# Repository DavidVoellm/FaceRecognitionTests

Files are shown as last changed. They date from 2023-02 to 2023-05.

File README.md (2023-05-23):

# **HAUS MIT SICHERHEITSTÜR**

NwT-Abschlussprojekt J2

Teilnehmer: Mona Endreß, Lutz Engler, Max Stacherowski, David Völlm

Zeitraum: 06.02.2023-22.05.2023



## **INHALTSVERZEICHNIS**

1. **Einleitung**                                                       3
1. **Vorbereitungsphase**                                               4
   1. Projektauftrag                                                    4
   1. Projektziele                                                      4
1. **Planungsphase**							                                 4
   1. Projektstrukturplan/ Arbeitspakete                                4
   1. Projektzeitplan                                                   5
   1. Recherche                                                         5
   1. Bauteile                                                          6
   1. Schaltung                                                         6
1. **Durchführungsphase**                                               7
   1. Funktionsbeschreibung                                             7
   1. Ablauf                                                            7
   1. Anhänge                                                           8
   1. Aufgabenbereiche                                                  8
1. **Abschlussphase**                                                   9
   1. Ist-Soll-Vergleich                                                9
   1. Fehleranalyse/ Verbesserungsvorschläge                            9
   1. Zusammenfassung/ Resümee                                          10
1. **Quellenangaben**                                                   10
   1. Literaturverzeichnis                                              10
   1. Internetquellenverzeichnis                                        10

##    **1. EINLEITUNG**

Wir wollen ein Miniaturhaus mit einer Sicherheitstüre bauen. Diese soll nur aufschließen, wenn eine Person anhand eines Gesichtserkennungsprogramms erkannt wird. 

Die Sicherheit und Privatsphäre gewann in den letzten Jahren immer mehr an Wichtigkeit und ist ein relevantes Thema für die Zukunft. Durch das wachsende Bewusstsein des Ersetzens von „altmodischen“ Begebenheiten durch neue Technologien, ist ein Fortschritt in allen Lebenssituationen unabdingbar. Das Leben der Menschen so effizient und unkompliziert wie möglich zu gestalten ist ein wichtiger Faktor im privaten Sektor. Bereits seit ein paar Jahren ist die Gesichtserkennung immer mehr bei Smartphones, Tablets usw. vertreten. Aber auch auf politischer, wirtschaftlicher und gesellschaftlicher Ebene gewinnt die künstliche Intelligenz beziehungsweise die Gesichtserkennung immer mehr an Bedeutung. So wird diese zum Beispiel für Massenüberwachungen, Zugangskontrollen oder die Suche nach Straftätern verwendet.  

1966 erschuf Woodrow „Woody“ Wilson Bledsoe eine Rechenmaschine, die „Computer-Person“, die die Anfänge der Gesichtserkennung mit Hilfe der künstlichen Intelligenz markierte. Das Grundprinzip einer solchen Maschine besteht daraus ein spezifisches Muster aus Bildern herauszufiltern und anschließend in binäre Codezeilen umzurechnen. Daraufhin wird diese Code-Kette mit einer Datenbank abgeglichen und über einen anderen Mechanismus an den Verbraucher signalisiert. Bei Woody zum Beispiel über einen angeschlossenen Ohrknopf. [\[1\]](https://www.boonedam.de/blog/das-gesicht-der-zukunft-erkennen#_ftn1) [\[4\]](https://www.boonedam.de/blog/das-gesicht-der-zukunft-erkennen#_ftn1) Das heißt die Gesichtserkennung ist kein neues Phänomen, sondern schon seit Jahrzehnten im stetigen Wandel. Nur hat sich die Funktionsweiße der Gesichtserkennung immer weiterentwickelt.

AnyVision ist der weltweit führende Entwickler von Computer Vision Software mit künstlicher Intelligenz für die Gesichtserkennung. „Die Mission von AnyVision ist es, künstliche Intelligenz weltweit zugänglich zu machen. Auf diese Weise entsteht ein Netzwerk intelligenter Geräte und setzt neue Standards für die Sicherheit in der Welt um uns herum“, erklärt Ray Brancato, Chief Revenue Officer bei AnyVision. [\[2\]](https://www.boonedam.de/blog/das-gesicht-der-zukunft-erkennen#_ftn1) So schön dieses Zitat von AnyVision klingt, die Gesichtserkennung hat auch ihre Schattenseiten. Regierungen können ihre Bevölkerung überwachen und kontrollieren und ein Verlust von Privatsphäre kann verstärkt auftreten. Ein Beispiel hierfür wäre China, wo Datenschutz über keine sonderliche Relevanz verfügt und die Bevölkerung quasi durchgehend überwacht wird. [\[3\]](https://www.boonedam.de/blog/das-gesicht-der-zukunft-erkennen#_ftn1) Auch sind Computersysteme im Vergleich zu Schlüssel und Schloss anfällig für Hackerangriffe. 

Deshalb möchten wir uns mit diesem Projekt damit beschäftigen die Gesichtserkennung so zu verwenden, dass die Privatsphäre der Menschen steigt und gleichzeitig eine Vereinfachung des Lebens stattfindet.

##    **2. VORBEREITUNGSPHASE**

### **2.1. Projektauftrag**

In einer Gruppe (2er-4er Teams) wird bis zum 22.05.2023 ein technisches Gerät entwickelt.

Das Projekt wird am 22.05.2023 präsentiert und die Dokumentation am 15.05.2023 fertiggestellt, ausgedruckt, digital und persönlich abgegeben. Ein erster Dokumentationsentwurf wird am 31.03.2023 abgegeben.

### **2.2. Projektziele**

Ein Haus mit Sicherheitstür soll erstellt werden. Die Tür kann nur durch ein Gesichtserkennungsprogramm nach außen geöffnet werden. Ein Knopf („Klingel“) startet das Programm und bei Erkennung einer Person öffnet sich das Schloss. Eine LED sowie ein Tonsignal eines Buzzers sollen angeben ob das Gesicht erkannt wurde und die Person berechtigt ist durchzugehen. 

##    **3. PLANUNGSPHASE**

### **3.1. Projektstrukturplan**



### **3.2. Projektzeitplan**

||<p>Woche 1</p><p>6/9.2.23</p>|<p>Woche 2</p><p>13/16.2.23</p>|<p>Woche 3</p><p>27\.2/2.3.23</p>|<p>Woche 4</p><p>6/9.3.23</p>|<p>Woche 5</p><p>13/16.3.23</p>|<p>Woche 6</p><p>20/23.3.23</p>|<p>Woche 7</p><p>27/30.3.23</p>|<p>Woche 8</p><p>8/11.5.23</p>|
| :- | :- | :- | :- | :- | :- | :- | :- | :- |
|Planung, Ideen|x|x|||||||
|**Programmierung**||x|x|x|x|x|x||
|Kamera|||x||||||
|**CAD**||x||x||x|x||
|**Dokumentation**|||x||||x|x|
|Testen||||||x||x|
|Sägen; Bohren|||||x||x||
|Zusammenbau||||||||x|
|Knopf||||||||x|

|**ABGABE**|<p>31\.03.2023</p><p>(Entwurf Dokumentation)</p>|<p>15\.05.2023</p><p>(Dokumentation)</p>|<p>22\.05.2023</p><p>(Präsentation)</p>|
| :-: | :-: | :-: | :-: |

### **3.3. Recherche:**

**Raspberry Pi: [\[5\]](https://www.boonedam.de/blog/das-gesicht-der-zukunft-erkennen#_ftn1)**

Der Raspberry Pi ist ein kostengünstiger (ca. 40€) kleiner Computer. Da er leider aktuell nicht mehr produziert wird, sind die wenigen übrigen Exemplare sehr teuer. Er wurde für die Universität Cambridge von der Raspberry Pi Foundation entwickelt. Es handelt sich um einen Einplatinen-Computer, der über kein Netzteil verfügt. Das passende Betriebssystem sind die Linux Distributionen.

Meistens wird dieser Mini-Computer als Steuerungs-Computer, Roboter-Komponente oder Multimedia-Center verwendet.

**Gesichtserkennung: [\[6\]](https://www.boonedam.de/blog/das-gesicht-der-zukunft-erkennen#_ftn1)**

„Die Gesichtserkennung ist ein Verfahren zur Identifizierung oder Bestätigung der Identität einer Person anhand ihres Gesichts. Gesichtserkennungssysteme können für die Bestimmung von Personen auf Fotos, in Videos oder in Echtzeit eingesetzt werden. Die Gesichtserkennung ist eine Kategorie der biometrischen Sicherheit.“

### **3.4. Bauteile**

Die verwendeten Bauteile können in 3 Bereiche unterteilt werden:

|**3D gedruckte Teile**|**Elektrische Bauteile**|**Andere**|
| :- | :- | :- |
|LED-Gehäuse|LED|2 x 250x180x5mm Holzplatte|
|Servo-Gehäuse|Knopf|2 x 250x150x5mm Holzplatte|
|Schloss (2-teilig)|Türsensor|2 x 180x150x5mm Holzplatte|
|Türgriff|Servo-Motor|4 x M3 30mm Schraube|
|Raspberry Pi Gehäuse|Buzzer (passiv)|4 x M3 Mutter|
|2 Scharniere|Lüfter|4 x M3 15mm Schraube|
|Tür Stopper|2 x 10kΩ Widerstand|4x M3 Mutter|
||220Ω Widerstand||
||Kabel||
||Raspberry Pi 4b (8GB)||
||Logitech Webcam 250||
||Netzteil (15W, 5V)||
||Micro HDMI-HDMI Adapter||
||USB Maus und Tastatur||
||Bildschirm (HDMI Anschluss)||

Die 3D gedruckten Teile finden sich alle unter dem [Ordner CAD](https://github.com/DavidVoellm/HouseWithFaceRecognition/tree/master/CAD), da drin sind auch die Technischen Zeichnungen.

### **3.5. Schaltung**



Die Schaltung wollten wir nicht mit einer Platine verwirklichen, da wir die Bauteile nicht direkt auf die Platine löten wollten und man auch keine Platine direkt auf den Raspberry Pi stecken kann.

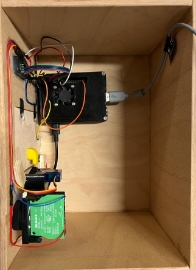
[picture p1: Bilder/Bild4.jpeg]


Durch zu kurze Kabel sind die Anschlüsse bei unserem Projekt etwas vertauscht: 
Knopf: 22; Servo: 27; Tür: 17; Buzzer: 26.
Der Rest bleibt gleich.

##    **4. DURCHFÜHRUNGSPHASE**

### **4.1. Funktionsbeschreibung**

Beim Starten des Programms, leuchtet die LED so lange orange, bis alle Initialisierungen fertig sind, dann leuchtet sie grün.

Während des Auf- und Zuschließvorgangs leuchtet die LED wieder orange, nach dem Aufschließen leuchtet sie dann grün und nach dem Zuschließen leuchtet sie rot.

Um die Gesichtserkennung zu starten, muss die Klingel gedrückt werden. Dann leuchtet die LED blau und es wird mit der Kamera ein Bild aufgenommen. Dieses wird nach bekannten Gesichtern untersucht. Wenn mindestens ein bekanntes Gesicht erkannt wird, wird die Türe aufgeschlossen, ansonsten piept der Alarm und die Türe bleibt verschlossen.

Neue Person hinzufügen (Mona, David): Wenn eine Person mit Zugriff die Türe aufschließt, aber noch nicht öffnet, kann eine neue Person hinzugefügt werden. Nach 2-sekündigem Drücken der Klingel beginnt die LED blau zu leuchten. Sobald die Klingel dann losgelassen wird, blinkt sie drei Mal blau und nach 1.5 Sekunden leuchtet die LED weiß. Jetzt wird eine neue Person hinzugefügt, sobald sich nur eine unbekannte Person im Bild befindet. Es kann pro Aufschließvorgang immer nur eine neue Person hinzugefügt werden und der ganze Vorgang kann immer durch ein kurzes Drücken der Klingel abgebrochen werden.

*(Das Programm lässt sich in dem Ordner [Software](https://github.com/DavidVoellm/HouseWithFaceRecognition/Software) dokumentiert vorfinden. Die Dateien in dem Ordner [Bibliotheken](https://github.com/DavidVoellm/HouseWithFaceRecognition/Software/Bibliotheken), stammen natürlich auch von uns und gehören zum Projekt.)*

**Eine Erklärung, wie das Programm zu starten ist, findet sich [hier](https://github.com/DavidVoellm/HouseWithFaceRecognition/blob/master/Wie%20starte%20ich%20das%20Programm.pdf).**

### **4.2. Ablauf**

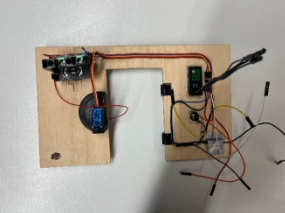
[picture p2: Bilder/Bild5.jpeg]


Wir haben damit begonnen, Testprogramme für die Gesichtserkennung zu schreiben, um zu wissen, ob unser Plan überhaupt möglich ist. Nachdem das funktioniert hat, haben wir das Betriebssystem Rasbian auf dem Raspberry Pi aufgesetzt. Dann haben wir angefangen 3D Modelle für Halterungen zu designen und einzelne elektrische Bauteile anzusteuern. Währenddessen hatten wir einige Schwierigkeiten bei der Kamera Auswahl, da einige nicht so funktioniert haben, wie es geplant war, deshalb haben wir schlussendlich eine USB-Webcam genommen. Als nächstes haben wir die Wände gesägt und zusammengeklebt und gleichzeitig die Gesamtschaltung gebaut und getestet. Mit dem Bau der Schaltung haben wir gleichzeitig das Programm angepasst und getestet. Dieses Teil hat den größten Teil des Projekts in Anspruch genommen. Als dieser Teil auch fertig war, kam der Zusammenbau, des gesamten Projekts, dazu gehörte das Verlöten der Schaltung, das Einbauen der elektrischen Bauteile in die Wand und das Anschließen der Kabel an den Raspberry Pi.

### **4.3. Anhänge**

Auf dem beigefügten Stick befinden sich die zusätzlichen Dateien (erklärter Programmcode, Frizzing, CAD-Komponenten, Nachbau der Boxteile in freeCAD…), die in der Dokumentation, um Dopplungen zu vermeiden, nicht eingefügt wurden (Alle diese Anhänge befinden sich aber auch aktualisiert auf [meinem GitHub Repo](https://github.com/DavidVoellm/HouseWithFaceRecognition)).

### **4.4. Aufgabenbereiche**
(Wer hat was gemacht)

 

##    **5. ABSCHLUSSPHASE**

### **5.1.Ist-Soll-Vergleich**

|**SOLL**|**IST**|
| :-: | :-: |
|Bis zu 22.05.2023 soll ein technisches Gerät entwickelt werden.|Am 22.05.2023 wurde das Projekt fertig abgegeben.|
|Ein Dokumentationsentwurf wird am 31.03.2023 abgegeben.|Ein Dokumentationsentwurf wurde am 31.03.2023 abgegeben.|
|Die vollständige Dokumentation wird am 15.05.2023 abgegeben.|Aufgrund von Verschiebungen der Unterrichtstunden wurde der Abgabetag auf den 22.05.2023 verlegt. Die Dokumentation wurde digital, ausgedruckt und abgegeben.|
|Eine Präsentation des Projektes findet am 22.05.2023 statt.|Die Präsentation wurde auf den 25.05.2023 verlegt.|
|Ein Haus mit Sicherheitstür soll erstellt werden. Die Tür kann verschlossen werden und wird nach außen geöffnet werden. Ein Knopf („Klingel“) startet das Programm und bei Erkennung einer Person öffnet sich das Schloss. |Eine Box, die wie ein Haus fungiert, mit Sicherheitstür wurde erstellt. Hierfür wurden die gestellten Ressourcen, CAD, Holz, usw., verwendet. Ein Knopf startet das Programm und es öffnet sich das Schloss. |
|Eine LED sowie ein Tonsignal eines Buzzers sollen angeben ob das Gesicht erkannt wurde und die Person berechtigt ist durchzugehen.|Die LED zeigt immer den Programmstatus an, aber der Buzzer ist beim Löten kaputt gegangen und funktioniert nicht mehr (Er hat zuvor aber funktioniert).|
|Es sollen Bauteilgehäuse gebaut werden.|Es wurde kein Buzzer Gehäuse gebaut, da es platztechnisch praktischer ohne war.|
|Eine passende Kamera soll ausgewählt werden.|Es wurde eine USB-Webcam ausgewählt.|
|Mit einer Kamera werden Bilder aufgenommen, die dann nach bekannten Personen untersucht werden.|Bilder können aufgenommen werden und ein System aus Bilderkennung und Personenhandler wertet diese aus. Neue Personen können hinzugefügt werden.|

### **5.2. Fehleranalyse und Verbesserungsvorschläge**

|**FEHLER**|**VERBESSERUNG**|
| :-: | :-: |
|Die Kameraauswertung ist manchmal fehlerhaft.|Kleine Toleranzwertveränderungen, aber Gesichtserkennung mit nur einem 2-dimensionalem Bild ist nicht sehr genau.|
|Der Raspberry Pi ist kaputt gegangen.|Es musste ein neuer gekauft werden.|
|Beim zusammenleimen der Holzplatten wurden die platten zu stark zusammengezogen und sie waren nicht mehr rechtwinklig zueinander.|Es wurde Holz dazwischen gesteckt, um die rechten Winkel zu bewahren.|
|Der Kleber war nicht stark genug, um manche 3D-Teile zu befestigen.|Es wurde ein Sekundenkleber besorgt.|
|Die Kamera wurde nicht erkannt|Es wurde eine andere USB-Kamera verwendet.|
|Türsensor erkennt nicht zuverlässig, ob die Türe geschlossen ist, da etwas Bewegungsspielraum frei ist.|Magneten halten die Tür geschlossen|

### **5.3. Zusammenfassung/ Resümee**

Das Ziel unseres Projektes war, kostengünstig und mit den von der Schule zur Verfügung gestellten Materialien ein Haus mit Sicherheitstür zu bauen. 

Dafür recherchierten wir zuerst die Relevanz der Gesichtserkennung in der heutigen Zeit. Tatsächlich ist die Gesichtserkennung in Bereichen wie z.B. dem Öffnen eines Smartphones viel vertreten. Jedoch wird sie noch selten für Haustüren verwendet. Wir wollten also herausfinden ob es im minimalistischen Stil wirksam ist ein Schloss mit Hilfe der Gesichtserkennung zu öffnen.

Durch den Bau unserer Box konnten wir dies erfolgreich durchführen und weitreichend testen. Eine LED zeigt immer den Programmstatus an, ein Türsensor erkennt, ob die Türe geschlossen wurde (und das Schloss nun verschlossen werden darf) und es können auch neue Personen, mit der Berechtigung „Schloss auf“ hinzuzugefügt werden.

##    **6. QUELLENANGABEN**

### **6.1. Literaturverzeichnis:**

   Verständnis von Neuronalen Netzen: [NNFS](https://nnfs.io/) Harrison Kinsley & Daniel Kukieła 

### **6.2. Internetquellenverzeichnis:**

1. <https://blog.boonedam.com> (06.03.2023) Larissa Wach: Das Gesicht der Zukunft erkennen. Meldung vom O.A.

<https://blog.boonedam.com/de-de/das-gesicht-der-zukunft-erkennen#_ftn1>

1. <https://niederlandenachrichten.de> (06.03.2023) Emma van Harten und Leandra Marzluff: Türhersteller und KI-Spezialist entwickeln intelligente Tür mit Gesichtserkennung. Meldung vom 06.08.2020

<https://niederlandenachrichten.de/fachartikel/turhersteller-und-ki-spezialist-entwickeln-intelligente-tur-mit-gesichtserkennung/>

1. <https://www.dr-datenschutz.de> (06.03.2023) anonymer Mitarbeiter: Die Zukunft der Gesichtserkennung. Meldung vom 07.09.2019

<https://www.dr-datenschutz.de/die-zukunft-der-gesichtserkennung/> 

1. <https://www.wired.com> (06.03.2023) Shaun Raviv: Secret history of facial recognition. Meldung vom 21.01.2020
1. <https://www.giga.de> (10.03.2023) Alexandra Kons: Was ist Raspberry Pi – einfach erklärt. Meldung vom 23.07.2020

https://www.giga.de/artikel/was-ist-raspberry-pi-einfach-erklaert--cwr5c2fqr7

1. <https://www.kaspersky.de> (10.03.2023) O.A.: Die Gesichtserkennung – Definition und Erläuterung. Meldung vom O.A.

https://www.kaspersky.de/resource-center/definitions/what-is-facial-recognition

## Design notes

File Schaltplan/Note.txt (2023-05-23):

geänderte Ports!

Knopf: 22
Servo: 27
Tür: 17

Buzzer: 26

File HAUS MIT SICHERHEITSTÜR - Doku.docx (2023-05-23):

HAUS MIT SICHERHEITSTÜR

NwT-Abschlussprojekt J2

Teilnehmer: Mona Endreß, Lutz Engler, Max Stacherowski, David Völlm

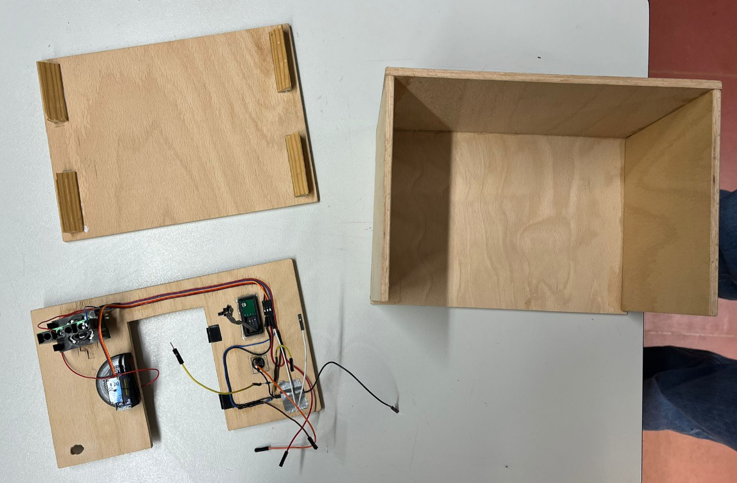
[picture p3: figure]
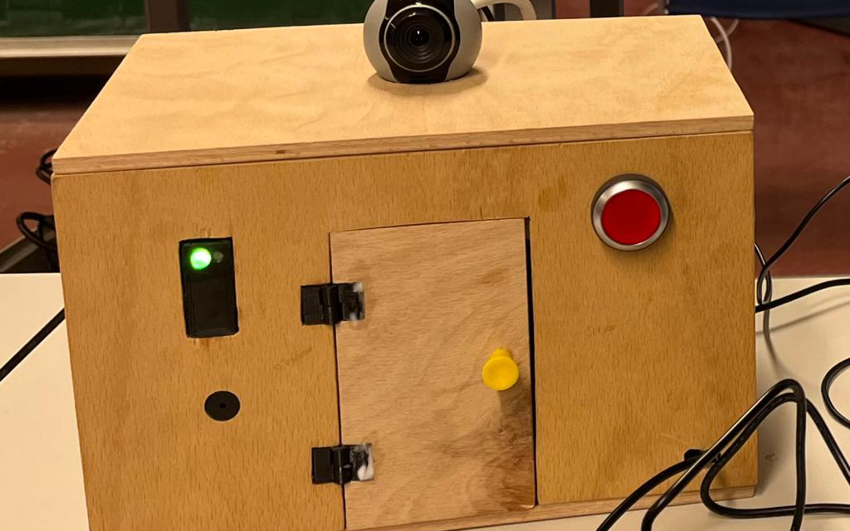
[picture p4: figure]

Zeitraum: 06.02.2023-22.05.2023

INHALTSVERZEICHNIS

1. Einleitung 3
2. Vorbereitungsphase 4
  2.1. Projektauftrag 4
  2.2. Projektziele 4
3. Planungsphase 4
  3.1. Projektstrukturplan/ Arbeitspakete 4
  3.2. Projektzeitplan 5
  3.3. Recherche 5
  3.4. Bauteile 6
  3.5. Schaltung 6
4. Durchführungsphase 7
  4.1. Funktionsbeschreibung 7
  4.2. Ablauf 7
  4.3. Anhänge 8
  4.4. Aufgabenbereiche 8
5. Abschlussphase 9
  5.1. Ist-Soll-Vergleich 9
  5.2. Fehleranalyse/ Verbesserungsvorschläge 9
  5.3. Zusammenfassung/ Resümee 10
6. Quellenangaben 10
  6.1. Literaturverzeichnis 10
  6.2. Internetquellenverzeichnis 10

1. EINLEITUNG

Wir wollen ein Miniaturhaus mit einer Sicherheitstüre bauen. Diese soll nur aufschließen, wenn eine Person anhand eines Gesichtserkennungsprogramms erkannt wird.

Die Sicherheit und Privatsphäre gewann in den letzten Jahren immer mehr an Wichtigkeit und ist ein relevantes Thema für die Zukunft. Durch das wachsende Bewusstsein des Ersetzens von „altmodischen“ Begebenheiten durch neue Technologien, ist ein Fortschritt in allen Lebenssituationen unabdingbar. Das Leben der Menschen so effizient und unkompliziert wie möglich zu gestalten ist ein wichtiger Faktor im privaten Sektor. Bereits seit ein paar Jahren ist die Gesichtserkennung immer mehr bei Smartphones, Tablets usw. vertreten. Aber auch auf politischer, wirtschaftlicher und gesellschaftlicher Ebene gewinnt die künstliche Intelligenz beziehungsweise die Gesichtserkennung immer mehr an Bedeutung. So wird diese zum Beispiel für Massenüberwachungen, Zugangskontrollen oder die Suche nach Straftätern verwendet.

1966 erschuf Woodrow „Woody“ Wilson Bledsoe eine Rechenmaschine, die „Computer-Person“, die die Anfänge der Gesichtserkennung mit Hilfe der künstlichen Intelligenz markierte. Das Grundprinzip einer solchen Maschine besteht daraus ein spezifisches Muster aus Bildern herauszufiltern und anschließend in binäre Codezeilen umzurechnen. Daraufhin wird diese Code-Kette mit einer Datenbank abgeglichen und über einen anderen Mechanismus an den Verbraucher signalisiert. Bei Woody zum Beispiel über einen angeschlossenen Ohrknopf. [1] (https://www.boonedam.de/blog/das-gesicht-der-zukunft-erkennen) [4] (https://www.boonedam.de/blog/das-gesicht-der-zukunft-erkennen) Das heißt die Gesichtserkennung ist kein neues Phänomen, sondern schon seit Jahrzehnten im stetigen Wandel. Nur hat sich die Funktionsweiße der Gesichtserkennung immer weiterentwickelt.

AnyVision ist der weltweit führende Entwickler von Computer Vision Software mit künstlicher Intelligenz für die Gesichtserkennung. „Die Mission von AnyVision ist es, künstliche Intelligenz weltweit zugänglich zu machen. Auf diese Weise entsteht ein Netzwerk intelligenter Geräte und setzt neue Standards für die Sicherheit in der Welt um uns herum“, erklärt Ray Brancato, Chief Revenue Officer bei AnyVision. [2] (https://www.boonedam.de/blog/das-gesicht-der-zukunft-erkennen) So schön dieses Zitat von AnyVision klingt, die Gesichtserkennung hat auch ihre Schattenseiten. Regierungen können ihre Bevölkerung überwachen und kontrollieren und ein Verlust von Privatsphäre kann verstärkt auftreten. Ein Beispiel hierfür wäre China, wo Datenschutz über keine sonderliche Relevanz verfügt und die Bevölkerung quasi durchgehend überwacht wird. [3] (https://www.boonedam.de/blog/das-gesicht-der-zukunft-erkennen) Auch sind Computersysteme im Vergleich zu Schlüssel und Schloss anfällig für Hackerangriffe.

Deshalb möchten wir uns mit diesem Projekt damit beschäftigen die Gesichtserkennung so zu verwenden, dass die Privatsphäre der Menschen steigt und gleichzeitig eine Vereinfachung des Lebens stattfindet.

2. VORBEREITUNGSPHASE

2.1. Projektauftrag

In einer Gruppe (2er-4er Teams) wird bis zum 22.05.2023 ein technisches Gerät entwickelt.

Das Projekt wird am 22.05.2023 präsentiert und die Dokumentation am 15.05.2023 fertiggestellt, ausgedruckt, digital und persönlich abgegeben. Ein erster Dokumentationsentwurf wird am 31.03.2023 abgegeben.

2.2. Projektziele

Ein Haus mit Sicherheitstür soll erstellt werden. Die Tür kann nur durch ein Gesichtserkennungsprogramm nach außen geöffnet werden. Ein Knopf („Klingel“) startet das Programm und bei Erkennung einer Person öffnet sich das Schloss. Eine LED sowie ein Tonsignal eines Buzzers sollen angeben ob das Gesicht erkannt wurde und die Person berechtigt ist durchzugehen.

3. PLANUNGSPHASE

3.1. Projektstrukturplan

Programm:

David & Max

- Gesichtserkennung

- Bauteile

- Ablauf

- Gesicht hinzufügen

- Tests

Aufbau:

Lutz

-Organisation & Übersicht
- Seitenwände & Dach
- Frontwand
- Elektronik

Dokumentation:

Mona

-Einleitung

-Vorbereitungsphase

-Planungsphase

-Durchführungsphase:

->Aufbau ->Durchführung

->Programmerkl.

…

-Abschlussphase

→Quellenverzeichnis

Präsentation:

Mona

-PowerPoint:

→Gestaltung & Struktur

→Einteilung

-Zusammen üben

-Vorbereitung Kolloquium

- Demo

Material:

Lutz

- Raspberry Pi (D)

- Kamera

- Holzwände

- elektrische Bauteile

Sonstiges:

David

-Schaltplan

- Technische Zeichnungen

CAD:

Max

- Servo

- Scharniere

- Gehäuse

Projektleitung Haus mit Sicherheitstür: David

3.2. Projektzeitplan

| Woche 1 6/9.2.23 | Woche 2 13/16.2.23 | Woche 3 27.2/2.3.23 | Woche 4 6/9.3.23 | Woche 5 13/16.3.23 | Woche 6 20/23.3.23 | Woche 7 27/30.3.23 | Woche 8 8/11.5.23
Planung, Ideen
Programmierung
Kamera
CAD
Dokumentation
Testen
Sägen; Bohren
Zusammenbau
Knopf

ABGABE | 31.03.2023 (Entwurf Dokumentation) | 15.05.2023 (Dokumentation) | 22.05.2023 (Präsentation)

3.3. Recherche:

Raspberry Pi: [5] (https://www.boonedam.de/blog/das-gesicht-der-zukunft-erkennen)

Der Raspberry Pi ist ein kostengünstiger (ca. 40€) kleiner Computer. Da er leider aktuell nicht mehr produziert wird, sind die wenigen übrigen Exemplare sehr teuer. Er wurde für die Universität Cambridge von der Raspberry Pi Foundation entwickelt. Es handelt sich um einen Einplatinen-Computer, der über kein Netzteil verfügt. Das passende Betriebssystem sind die Linux Distributionen.

Meistens wird dieser Mini-Computer als Steuerungs-Computer, Roboter-Komponente oder Multimedia-Center verwendet.

Gesichtserkennung: [6] (https://www.boonedam.de/blog/das-gesicht-der-zukunft-erkennen)

„Die Gesichtserkennung ist ein Verfahren zur Identifizierung oder Bestätigung der Identität einer Person anhand ihres Gesichts. Gesichtserkennungssysteme können für die Bestimmung von Personen auf Fotos, in Videos oder in Echtzeit eingesetzt werden. Die Gesichtserkennung ist eine Kategorie der biometrischen Sicherheit.“

3.4. Bauteile

Die verwendeten Bauteile können in 3 Bereiche unterteilt werden:

3D gedruckte Teile | Elektrische Bauteile | Andere
LED-Gehäuse | LED | 2 x 250x180x5mm Holzplatte
Servo-Gehäuse | Knopf | 2 x 250x150x5mm Holzplatte
Schloss (2-teilig) | Türsensor | 2 x 180x150x5mm Holzplatte
Türgriff | Servo-Motor | 4 x M3 30mm Schraube
Raspberry Pi Gehäuse | Buzzer (passiv) | 4 x M3 Mutter
2 Scharniere | Lüfter | 4 x M3 15mm Schraube
Tür Stopper | 2 x 10kΩ Widerstand | 4x M3 Mutter
| 220Ω Widerstand
| Kabel
| Raspberry Pi 4b (8GB)
| Logitech Webcam 250
| Netzteil (15W, 5V)
| Micro HDMI-HDMI Adapter
| USB Maus und Tastatur
| Bildschirm (HDMI Anschluss)

Die 3D gedruckten Teile finden sich alle unter dem Ordner CAD (https://github.com/DavidVoellm/HouseWithFaceRecognition/tree/master/CAD), da drin sind auch die Technischen Zeichnungen.

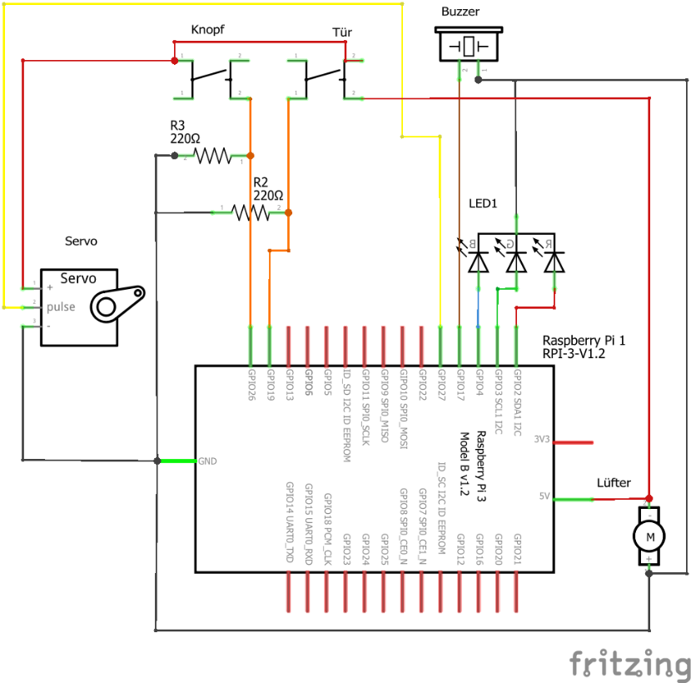
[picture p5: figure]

3.5. Schaltung

Die Schaltung wollten wir nicht mit einer Platine verwirklichen, da wir die Bauteile nicht direkt auf die Platine löten wollten und man auch keine Platine direkt auf den Raspberry Pi stecken kann.

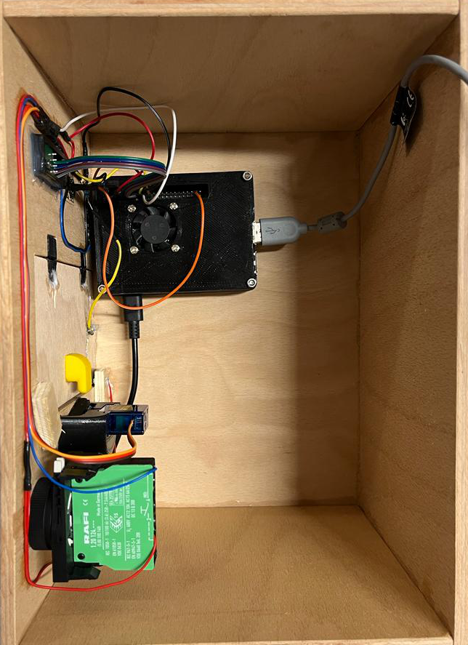
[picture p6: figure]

Durch zu kurze Kabel sind die Anschlüsse bei unserem Projekt etwas vertauscht:
Knopf: 22; Servo: 27; Tür: 17; Buzzer: 26
Der Rest bleibt gleich.

4. DURCHFÜHRUNGSPHASE

4.1. Funktionsbeschreibung

Beim Starten des Programms, leuchtet die LED so lange orange, bis alle Initialisierungen fertig sind, dann leuchtet sie grün.

Während des Auf- und Zuschließvorgangs leuchtet die LED wieder orange, nach dem Aufschließen leuchtet sie dann grün und nach dem Zuschließen leuchtet sie rot.

Um die Gesichtserkennung zu starten, muss die Klingel gedrückt werden. Dann leuchtet die LED blau und es wird mit der Kamera ein Bild aufgenommen. Dieses wird nach bekannten Gesichtern untersucht. Wenn mindestens ein bekanntes Gesicht erkannt wird, wird die Türe aufgeschlossen, ansonsten piept der Alarm und die Türe bleibt verschlossen.

Neue Person hinzufügen (Mona, David): Wenn eine Person mit Zugriff die Türe aufschließt, aber noch nicht öffnet, kann eine neue Person hinzugefügt werden. Nach 2-sekündigem Drücken der Klingel beginnt die LED blau zu leuchten. Sobald die Klingel dann losgelassen wird, blinkt sie drei Mal blau und nach 1.5 Sekunden leuchtet die LED weiß. Jetzt wird eine neue Person hinzugefügt, sobald sich nur eine unbekannte Person im Bild befindet. Es kann pro Aufschließvorgang immer nur eine neue Person hinzugefügt werden und der ganze Vorgang kann immer durch ein kurzes Drücken der Klingel abgebrochen werden.

(Das Programm lässt sich in dem Ordner Software (https://github.com/DavidVoellm/HouseWithFaceRecognition/Software) dokumentiert vorfinden. Die Dateien in dem Ordner Bibliotheken (https://github.com/DavidVoellm/HouseWithFaceRecognition/Software/Bibliotheken), stammen natürlich auch von uns und gehören zum Projekt.)

Eine Erklärung, wie das Programm zu starten ist, findet sich hier (https://github.com/DavidVoellm/HouseWithFaceRecognition/blob/master/Wie%20starte%20ich%20das%20Programm.pdf).

4.2. Ablauf

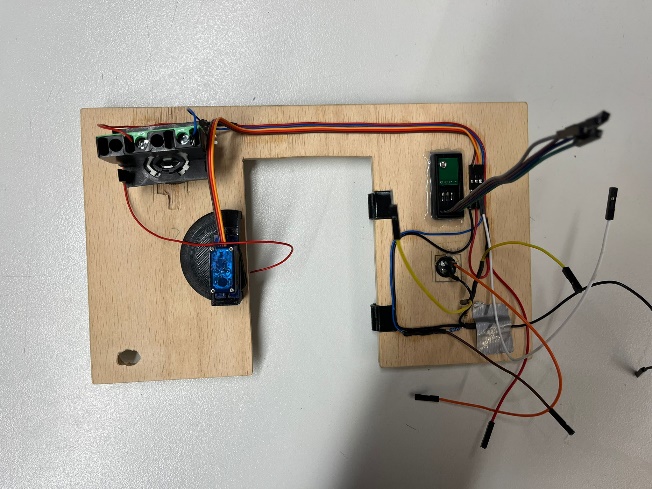
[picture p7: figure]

Wir haben damit begonnen, Testprogramme für die Gesichtserkennung zu schreiben, um zu wissen, ob unser Plan überhaupt möglich ist. Nachdem das funktioniert hat, haben wir das Betriebssystem Rasbian auf dem Raspberry Pi aufgesetzt. Dann haben wir angefangen 3D Modelle für Halterungen zu designen und einzelne elektrische Bauteile anzusteuern. Währenddessen hatten wir einige Schwierigkeiten bei der Kamera Auswahl, da einige nicht so funktioniert haben, wie es geplant war, deshalb haben wir schlussendlich eine USB-Webcam genommen. Als nächstes haben wir die Wände gesägt und zusammengeklebt und gleichzeitig die Gesamtschaltung gebaut und getestet. Mit dem Bau der Schaltung haben wir gleichzeitig das Programm angepasst und getestet. Dieses Teil hat den größten Teil des Projekts in Anspruch genommen. Als dieser Teil auch fertig war, kam der Zusammenbau, des gesamten Projekts, dazu gehörte das Verlöten der Schaltung, das Einbauen der elektrischen Bauteile in die Wand und das Anschließen der Kabel an den Raspberry Pi.

4.3. Anhänge

Auf dem beigefügten Stick befinden sich die zusätzlichen Dateien (erklärter Programmcode, Frizzing, CAD-Komponenten, Nachbau der Boxteile in freeCAD…), die in der Dokumentation, um Dopplungen zu vermeiden, nicht eingefügt wurden (Alle diese Anhänge befinden sich aber auch aktualisiert auf meinem GitHub Repo (https://github.com/DavidVoellm/HouseWithFaceRecognition)).

4.4. Aufgabenbereiche (Wer hat was gemacht)

Programm:

David & Max

- Gesichts-erkennung (D&Ma)

- Buzzer (L)

- LED (D)

- Knopf (Ma&L)

- Ablauf (Ma&D)

- Gesicht hinzufügen (D&Mo)

- Struktur (D)

- Tests (D)

Aufbau:

Lutz

-Organisation & Übersicht (L)
-Seitenwände (Mo&L&Ma)
- Dach (L&Ma)
- Frontwand (D)
- löten (D&L)
- Elektronik (D)

Dokumentation:

Mona

-Einleitung (Mo)

-Vorbereitungsphase (Mo)

-Planungsphase (Mo&D)

-Durchführungsphase

(D):

Aufbau & Durchführung (D&L)

Programmerkl.(D)

Programmdokumentation (D)

…

-Abschlussphase (Ma)

→Quellenverzeichnis (Mo)

Präsentation:

Mona

-PowerPoint:

→Informationen Auswahl (alle)

→Gestaltung & Struktur (alle)

→Einteilung (Mo)

-Stichwortzettel (alle)

-Haus zeigen (L)

-Abspeicherung (alle)

-Vorstellung (alle)

-Zusammen üben (alle)

-Vorbereitung Kolloquium (alle)

Material:

Lutz

- Holz (L&Mo)

-Aufbewahrung (Schule&D)

- Raspberry Pi (D)

- Kamera (Ma)

Sonstiges:

David

-Schaltplan (D)

- Technische Zeichnungen (D)

CAD:

Max

- Servo (Ma)

- Scharniere (Mo&L)

- Buzzer Gehäuse (L) weggelassen!

- Raspberry Gehäuse (D)

- LED-Gehäuse (D)

Projektleitung Haus mit Sicherheitstür: David

5. ABSCHLUSSPHASE

5.1.Ist-Soll-Vergleich

SOLL | IST
Bis zu 22.05.2023 soll ein technisches Gerät entwickelt werden. | Am 22.05.2023 wurde das Projekt fertig abgegeben.
Ein Dokumentationsentwurf wird am 31.03.2023 abgegeben. | Ein Dokumentationsentwurf wurde am 31.03.2023 abgegeben.
Die vollständige Dokumentation wird am 15.05.2023 abgegeben. | Aufgrund von Verschiebungen der Unterrichtstunden wurde der Abgabetag auf den 22.05.2023 verlegt. Die Dokumentation wurde digital, ausgedruckt und abgegeben.
Eine Präsentation des Projektes findet am 22.05.2023 statt. | Die Präsentation wurde auf den 25.05.2023 verlegt.
Ein Haus mit Sicherheitstür soll erstellt werden. Die Tür kann verschlossen werden und wird nach außen geöffnet werden. Ein Knopf („Klingel“) startet das Programm und bei Erkennung einer Person öffnet sich das Schloss. | Eine Box, die wie ein Haus fungiert, mit Sicherheitstür wurde erstellt. Hierfür wurden die gestellten Ressourcen, CAD, Holz, usw., verwendet. Ein Knopf startet das Programm und es öffnet sich das Schloss.
Eine LED sowie ein Tonsignal eines Buzzers sollen angeben ob das Gesicht erkannt wurde und die Person berechtigt ist durchzugehen. | Die LED zeigt immer den Programmstatus an, aber der Buzzer ist beim Löten kaputt gegangen und funktioniert nicht mehr (Er hat zuvor aber funktioniert).
Es sollen Bauteilgehäuse gebaut werden. | Es wurde kein Buzzer Gehäuse gebaut, da es platztechnisch praktischer ohne war.
Eine passende Kamera soll ausgewählt werden. | Es wurde eine USB-Webcam ausgewählt.
Mit einer Kamera werden Bilder aufgenommen, die dann nach bekannten Personen untersucht werden. | Bilder können aufgenommen werden und ein System aus Bilderkennung und Personenhandler wertet diese aus. Neue Personen können hinzugefügt werden.

5.2. Fehleranalyse und Verbesserungsvorschläge

FEHLER | VERBESSERUNG
Die Kameraauswertung ist manchmal fehlerhaft. | Kleine Toleranzwertveränderungen, aber Gesichtserkennung mit nur einem 2-dimensionalem Bild ist nicht sehr genau.
Der Raspberry Pi ist kaputt gegangen. | Es musste ein neuer gekauft werden.
Beim zusammenleimen der Holzplatten wurden die platten zu stark zusammengezogen und sie waren nicht mehr rechtwinklig zueinander. | Es wurde Holz dazwischen gesteckt, um die rechten Winkel zu bewahren.
Der Kleber war nicht stark genug, um manche 3D-Teile zu befestigen. | Es wurde ein Sekundenkleber besorgt.
Die Kamera wurde nicht erkannt | Es wurde eine andere USB-Kamera verwendet.
Türsensor erkennt nicht zuverlässig, ob die Türe geschlossen ist, da etwas Bewegungsspielraum frei ist. | Magneten halten die Tür geschlossen

5.3. Zusammenfassung/ Resümee

Das Ziel unseres Projektes war, kostengünstig und mit den von der Schule zur Verfügung gestellten Materialien ein Haus mit Sicherheitstür zu bauen.

Dafür recherchierten wir zuerst die Relevanz der Gesichtserkennung in der heutigen Zeit. Tatsächlich ist die Gesichtserkennung in Bereichen wie z.B. dem Öffnen eines Smartphones viel vertreten. Jedoch wird sie noch selten für Haustüren verwendet. Wir wollten also herausfinden ob es im minimalistischen Stil wirksam ist ein Schloss mit Hilfe der Gesichtserkennung zu öffnen.

Durch den Bau unserer Box konnten wir dies erfolgreich durchführen und weitreichend testen. Eine LED zeigt immer den Programmstatus an, ein Türsensor erkennt, ob die Türe geschlossen wurde (und das Schloss nun verschlossen werden darf) und es können auch neue Personen, mit der Berechtigung „Schloss auf“ hinzuzugefügt werden.

6. QUELLENANGABEN

7.1. Literaturverzeichnis:

Verständnis von Neuronalen Netzen: NNFS (https://nnfs.io/) Harrison Kinsley & Daniel Kukieła

7.2. Internetquellenverzeichnis:

[1] https://blog.boonedam.com (06.03.2023) Larissa Wach: Das Gesicht der Zukunft erkennen. Meldung vom O.A.

https://blog.boonedam.com/de-de/das-gesicht-der-zukunft-erkennen#_ftn1

[2] https://niederlandenachrichten.de (06.03.2023) Emma van Harten und Leandra Marzluff: Türhersteller und KI-Spezialist entwickeln intelligente Tür mit Gesichtserkennung. Meldung vom 06.08.2020

https://niederlandenachrichten.de/fachartikel/turhersteller-und-ki-spezialist-entwickeln-intelligente-tur-mit-gesichtserkennung/

[3] https://www.dr-datenschutz.de (06.03.2023) anonymer Mitarbeiter: Die Zukunft der Gesichtserkennung. Meldung vom 07.09.2019

https://www.dr-datenschutz.de/die-zukunft-der-gesichtserkennung/

[4] https://www.wired.com (06.03.2023) Shaun Raviv: Secret history of facial recognition. Meldung vom 21.01.2020
[5] https://www.giga.de (10.03.2023) Alexandra Kons: Was ist Raspberry Pi – einfach erklärt. Meldung vom 23.07.2020

https://www.giga.de/artikel/was-ist-raspberry-pi-einfach-erklaert--cwr5c2fqr7

[6] https://www.kaspersky.de (10.03.2023) O.A.: Die Gesichtserkennung – Definition und Erläuterung. Meldung vom O.A.

https://www.kaspersky.de/resource-center/definitions/what-is-facial-recognition

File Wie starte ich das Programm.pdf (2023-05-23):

## Wie starte ich das Programm?

Schritt 1:

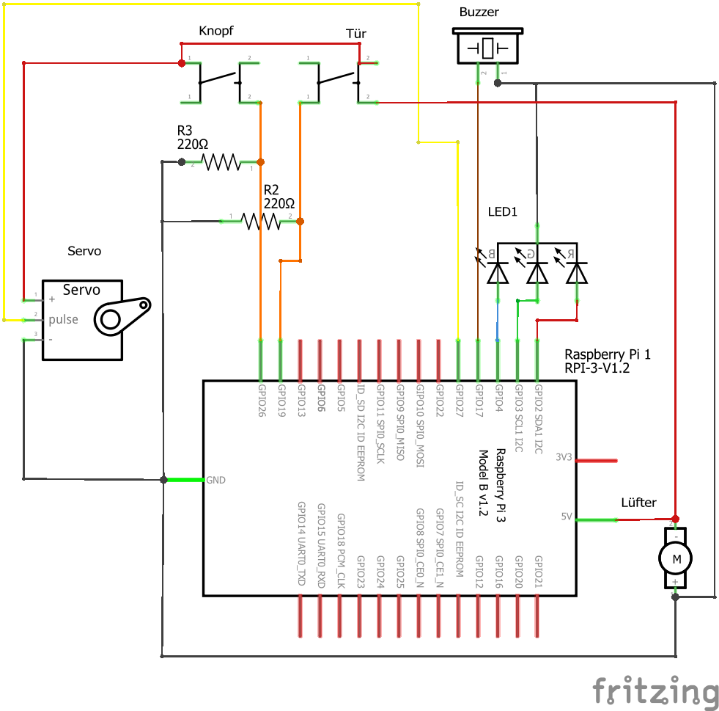
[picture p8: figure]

Um das Programm starten zu können müssen zuerst alle Kabel an den Raspberry Pi angeschlossen werden.

Durch zu kurze Kabel sind die Anschlüsse bei unserem Projekt etwas vertauscht:
Knopf: 22;
Servo: 27;
Tür: 17;
Buzzer: 26
Der Rest
bleibt gleich.

Schritt 2:

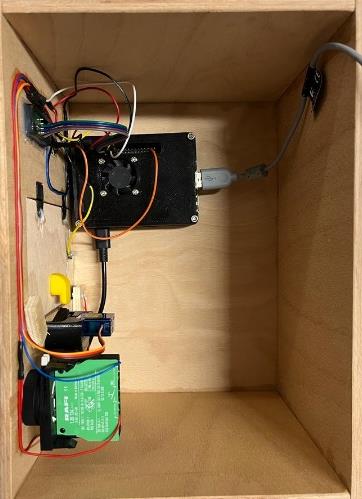
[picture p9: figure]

Als nächstes muss der Bildschirm und die Maus angeschlossen werden, dazu kann die Maus einfach in einen beliebigen USB-Port eingesteckt werden und der Bildschirm kann über einen Micro HDMI Adapter an die Seite neben die Stromversorgung angeschlossen werden. Optional kann zu der Maus auch noch eine Tastatur angeschlossen werden.
Schritt 3:

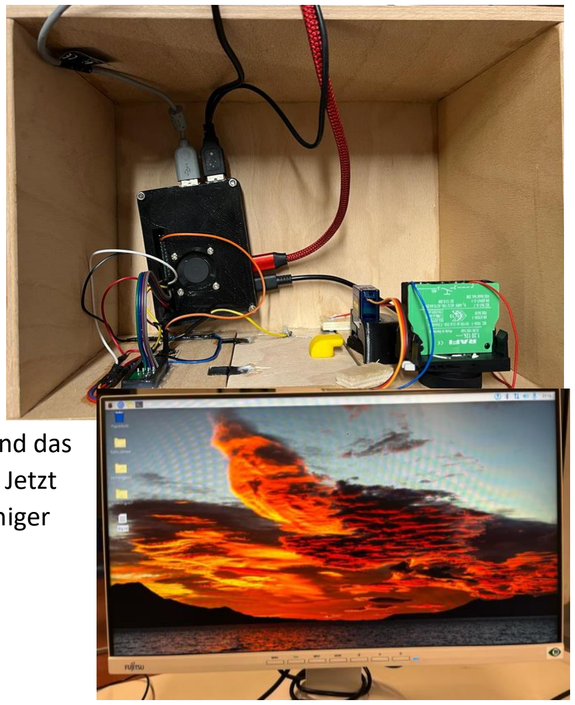
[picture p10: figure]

Schritt drei besteht darin, den Bildschirm und das Netzteil für den Raspberry Pi einzustecken. Jetzt sollte der Raspberry Pi booten und nach einiger Zeit zeigt der Bildschirm den Desktop.

Schritt 4:

Nun öffnet man das Dateisystem über den gelben Ordner oben links

Schritt 5:

Hier geht man über den Ordner NwT-Projekt.

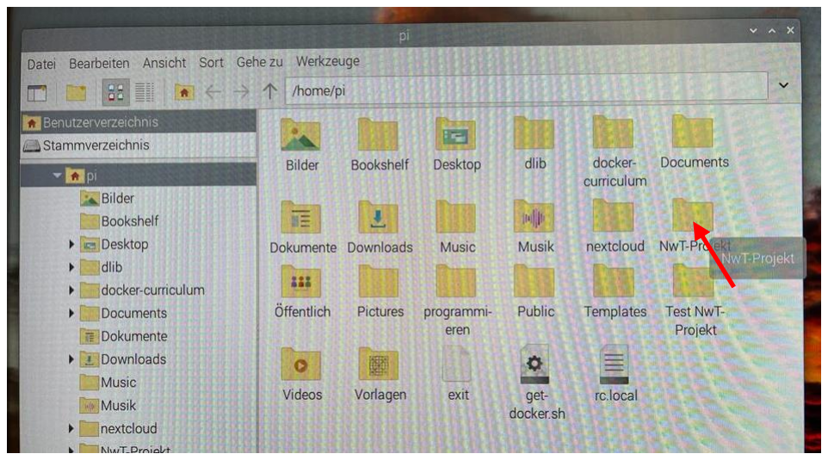
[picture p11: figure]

In den Ordner Software.

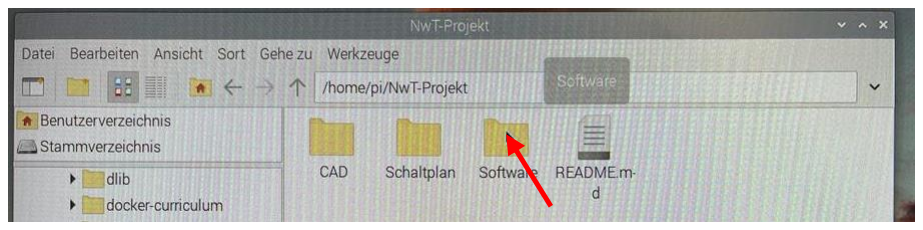
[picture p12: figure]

Schritt 6:

Dort klickt man mit der rechten Maustaste auf die Datei main.py.

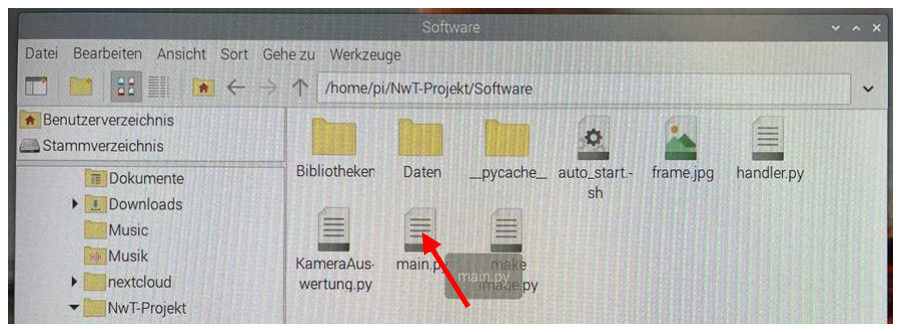
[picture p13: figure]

Und wählt Thonny aus.

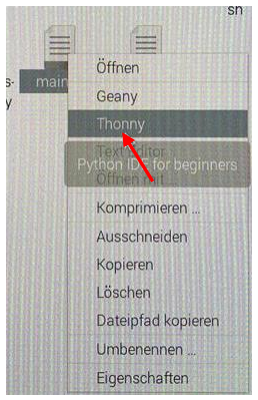
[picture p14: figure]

Schritt 7:

Jetzt öffnet sich das Programmfenster und mit einem Klick auf den „Run“-Button wird das Programm gestartet.

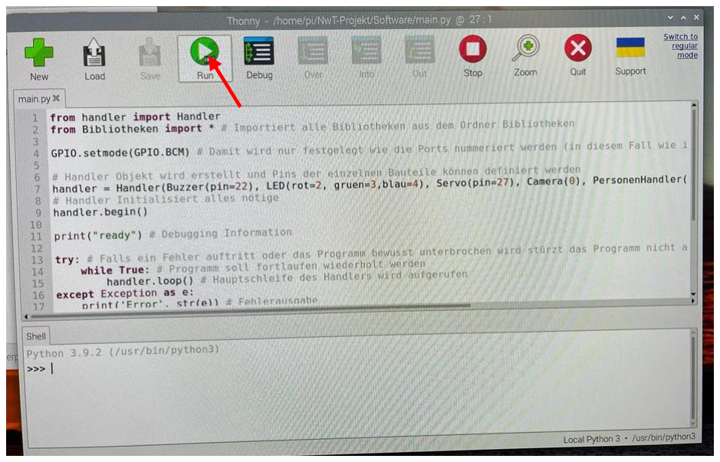
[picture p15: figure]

Sobald in der Ausgabe „ready“ erscheint, ist das Programm einsatzbereit. Der Bildschirm und die Maus können jetzt problemlos entfernt werden.

## Wie beende ich das Programm wieder?

Schritt 1:

Das Programm selbst lässt sich über den „Stop“-Button wieder beenden und kann natürlich auch wieder über den „Run“-Button erneut gestartet werden.

Wenn man aber fertig mit der Benutzung sein sollte, so muss der Raspberry Pi wieder heruntergefahren werden. Dazu klickt man auf das Raspberry Pi Symbol oben links

Und wählt erst die Option „Abmelden“

Und dann die Option „herunterfahren“

Schritt 2:

Nachdem der Bildschirm ausgegangen ist und man noch kurz gewartet hat, kann das Netzteil des Raspberry Pi’s wieder ausgesteckt werden.

(Falls der Bildschirm zwischendrin entfernt wurde, kann auch Schritt 1 weggelassen werden und es wird nur der Raspberry Pi vom Strom getrennt. Es sollte nichts kaputt gehen, aber es ist nicht empfohlen)

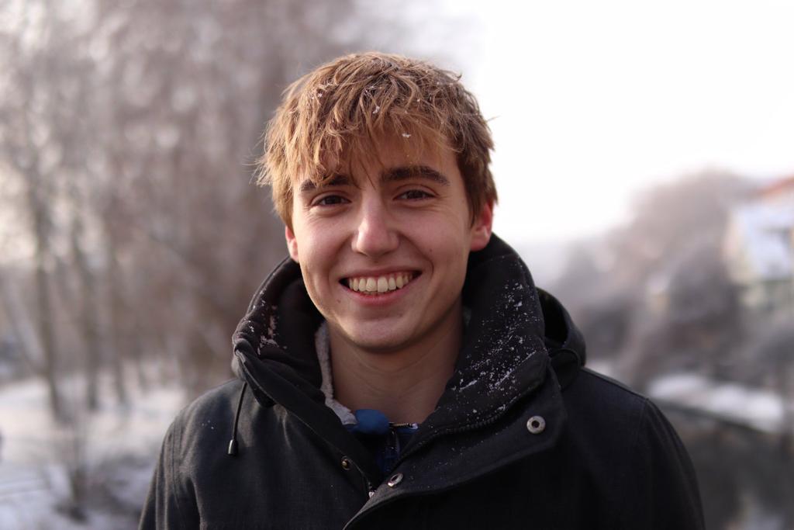
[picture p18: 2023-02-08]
Software/Daten/David.jpg

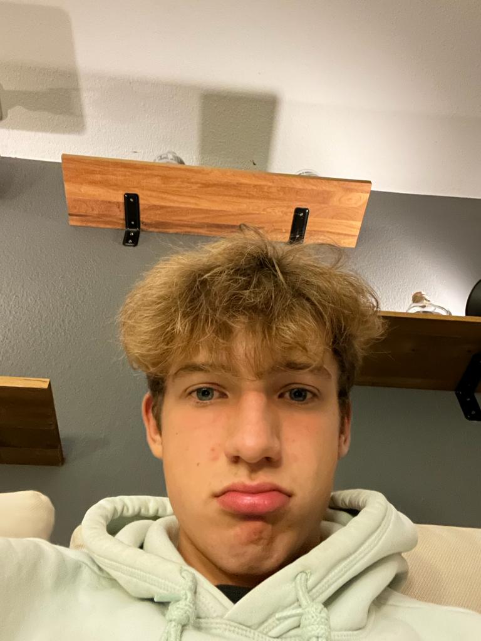
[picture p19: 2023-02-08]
Software/Daten/Philipp.jpg

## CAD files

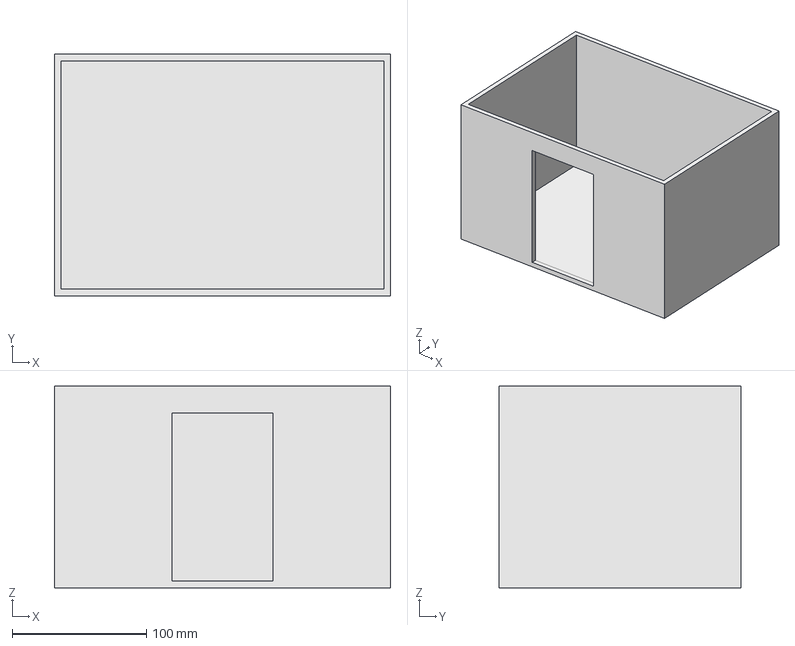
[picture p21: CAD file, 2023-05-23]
CAD/Haus (Lutz)/Haus.FCStd
250.0 x 180.0 x 150.0 mm

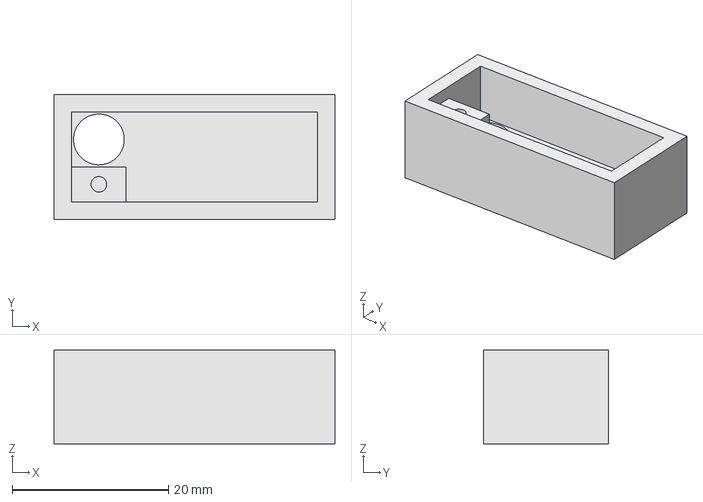
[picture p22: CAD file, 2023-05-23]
CAD/LED (David)/LED Halterung.FCStd
36.0 x 16.0 x 12.0 mm

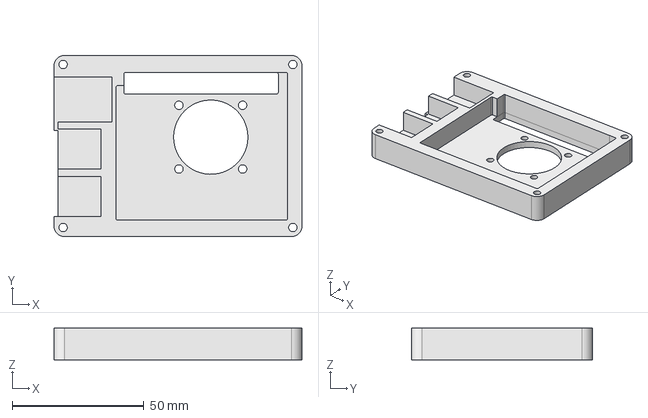
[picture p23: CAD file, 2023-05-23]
CAD/Raspberry (David)/1. Lage.FCStd
94.0 x 68.7 x 12.0 mm

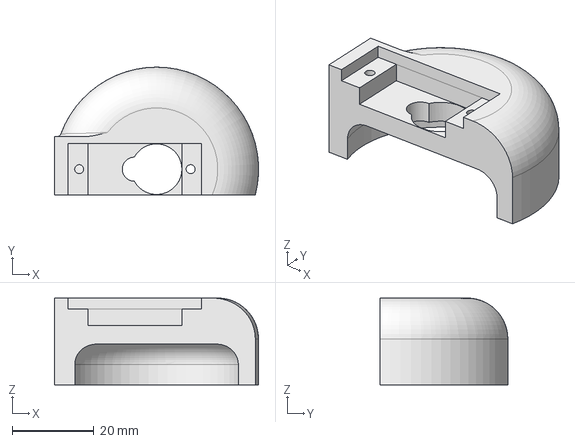
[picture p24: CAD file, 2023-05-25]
CAD/Servo (David)/Servohalter.FCStd
50.0 x 31.3 x 21.3 mm

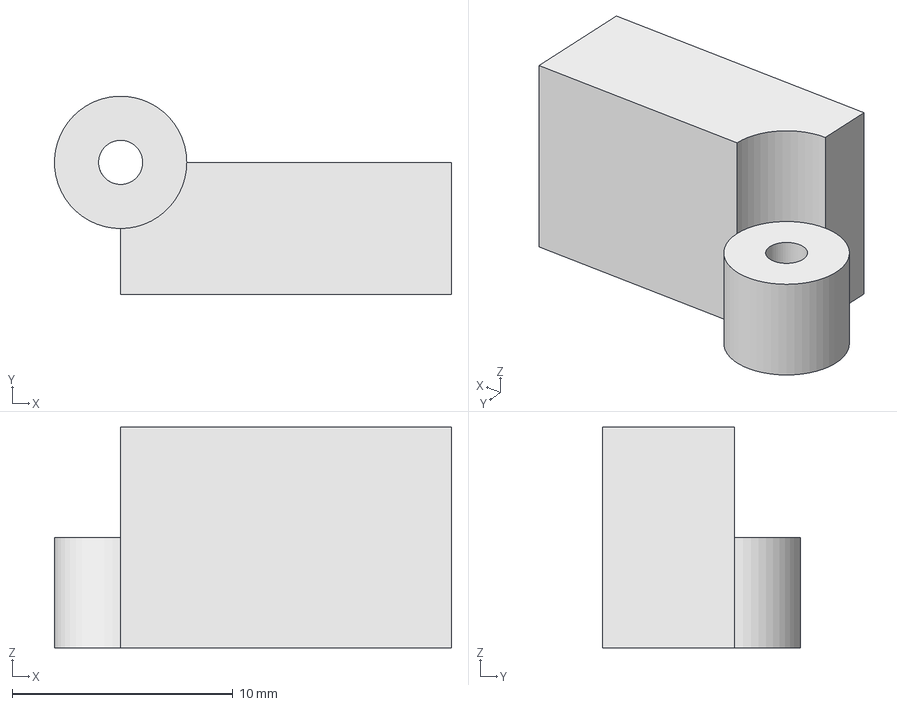
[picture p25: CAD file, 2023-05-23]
CAD/Tür (Max, Mona)/Schaniere (Mona Lutz)/Schanier.FCStd
18.0 x 9.00 x 10.0 mm

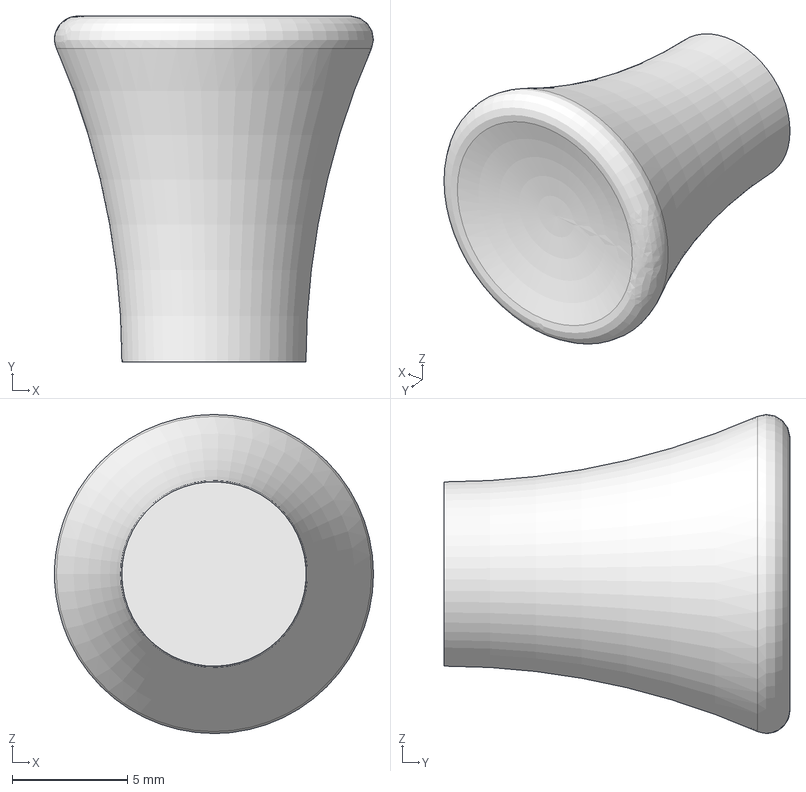
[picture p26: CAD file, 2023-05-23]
CAD/Tür (Max, Mona)/Türknauf (Max)/Türknauf.FCStd
13.8 x 15.0 x 13.8 mm

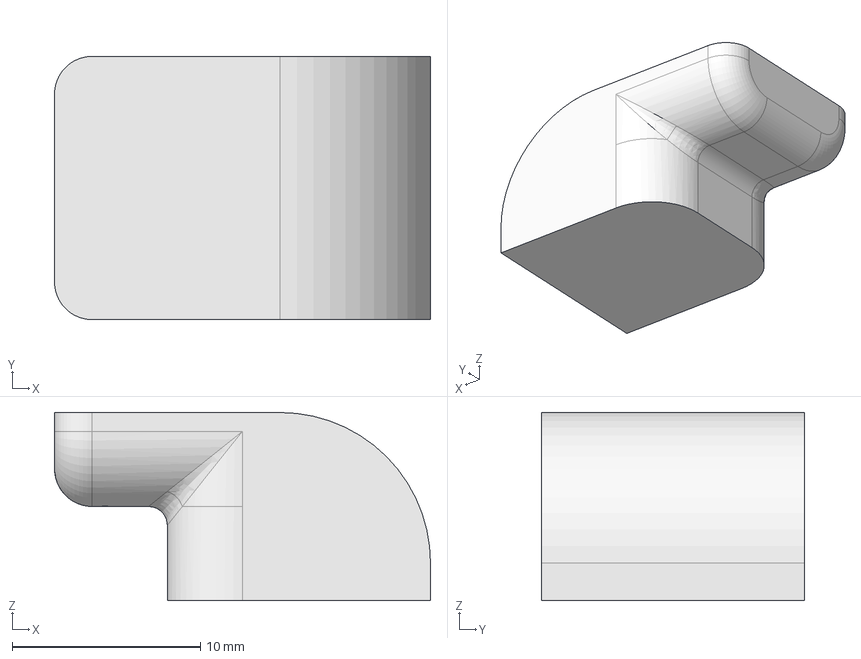
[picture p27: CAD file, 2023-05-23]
CAD/Tür (Max, Mona)/Türschloss (Max)/Türschloss Teil 2.FCStd
20.0 x 14.0 x 10.0 mm

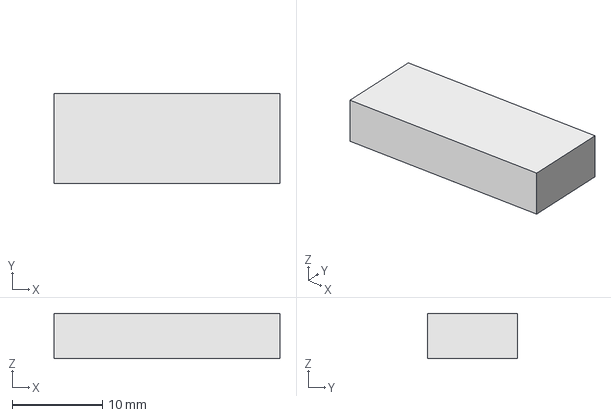
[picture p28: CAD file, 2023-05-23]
CAD/Tür (Max, Mona)/Türstopper (Max)/Türstopper.FCStd
25.0 x 10.0 x 5.00 mm

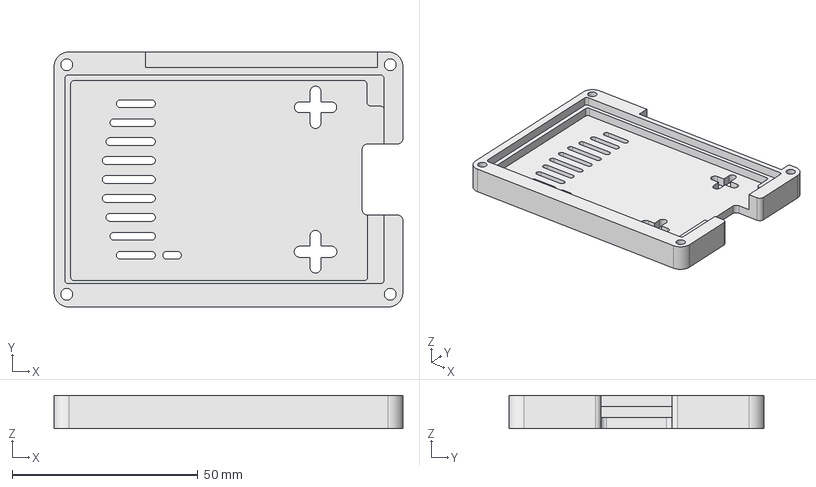
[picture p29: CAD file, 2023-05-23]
CAD/Raspberry (David)/3. Lage.FCStd
94.0 x 68.7 x 9.00 mm

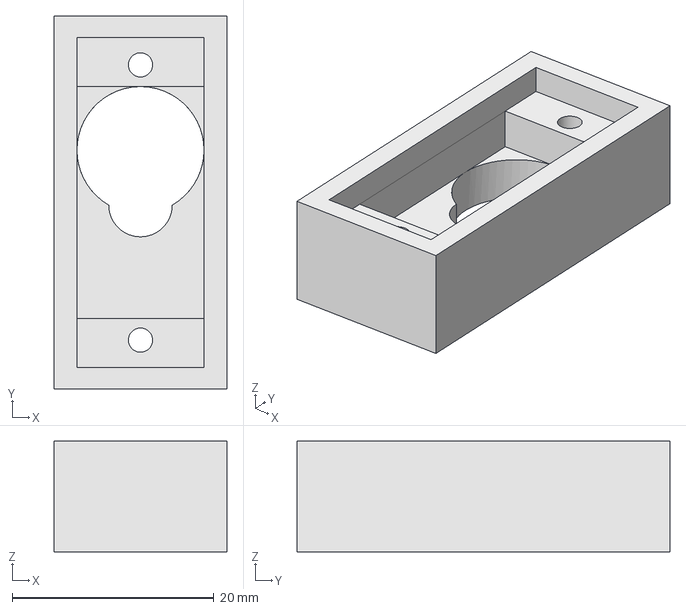
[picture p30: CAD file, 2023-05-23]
CAD/Servo (David)/Servohalterung.FCStd
17.1 x 37.0 x 11.0 mm

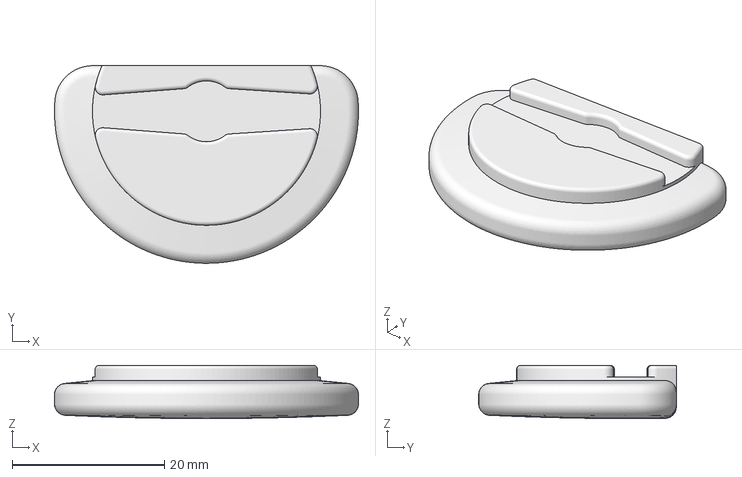
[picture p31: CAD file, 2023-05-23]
CAD/Tür (Max, Mona)/Türschloss (Max)/Türschloss Teil 1.FCStd
40.0 x 26.0 x 7.00 mm

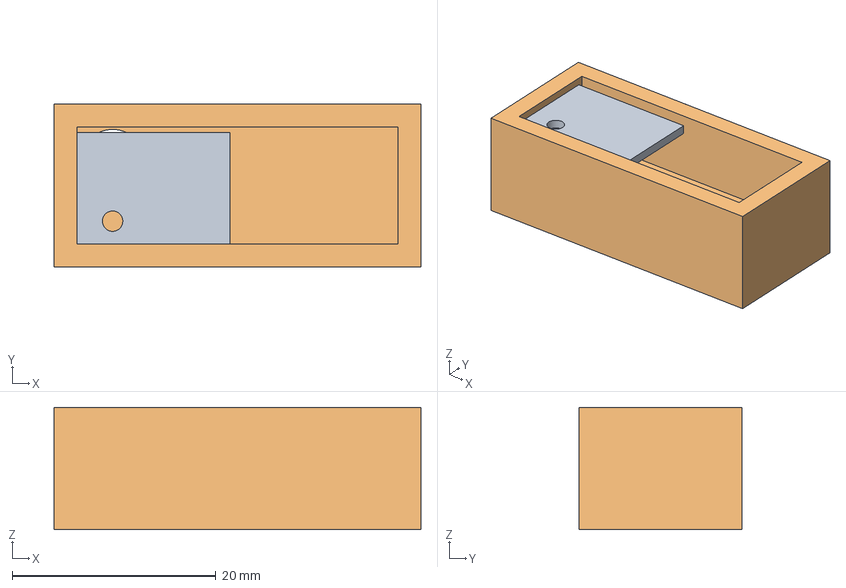
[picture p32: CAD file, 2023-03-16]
CAD/LED (David)/LED Zusammenbau.FCStd
36.0 x 16.0 x 12.0 mm
LED_001
LED Halterung_001

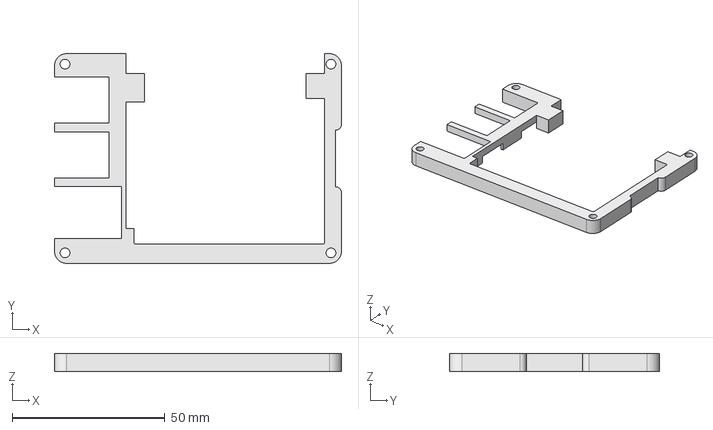
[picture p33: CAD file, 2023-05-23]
CAD/Raspberry (David)/2. Lage.FCStd
94.0 x 68.7 x 6.00 mm

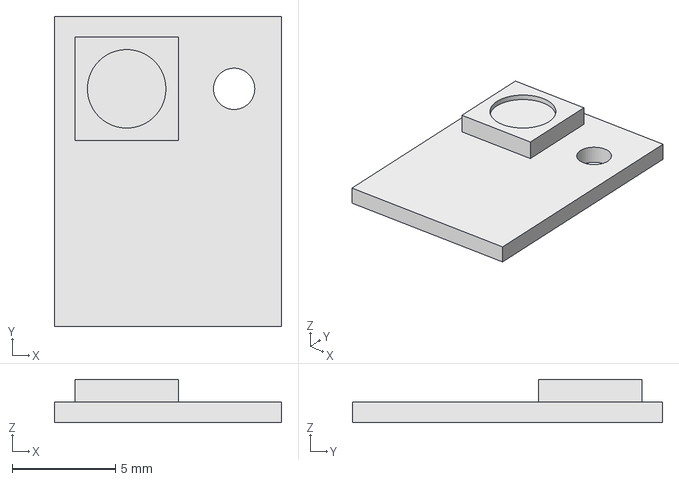
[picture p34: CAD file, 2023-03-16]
CAD/LED (David)/LED.FCStd
11.0 x 15.0 x 2.10 mm

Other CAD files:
CAD/LED (David)/LED Halterung-Body.stl
CAD/Servo (David)/Servohalterung-Body.stl
CAD/Raspberry (David)/Grundlage.FCStd
CAD/Servo (David)/Servo_Zusammenbau.FCStd
CAD/Raspberry (David)/1. Lage-Body.stl
CAD/Raspberry (David)/2. Lage-Body.stl
CAD/Raspberry (David)/3. Lage-Body.stl
CAD/Servo (David)/Servo.FCStd
CAD/Tür (Max, Mona)/Türschloss (Max)/Türschloss Teil 1.stl

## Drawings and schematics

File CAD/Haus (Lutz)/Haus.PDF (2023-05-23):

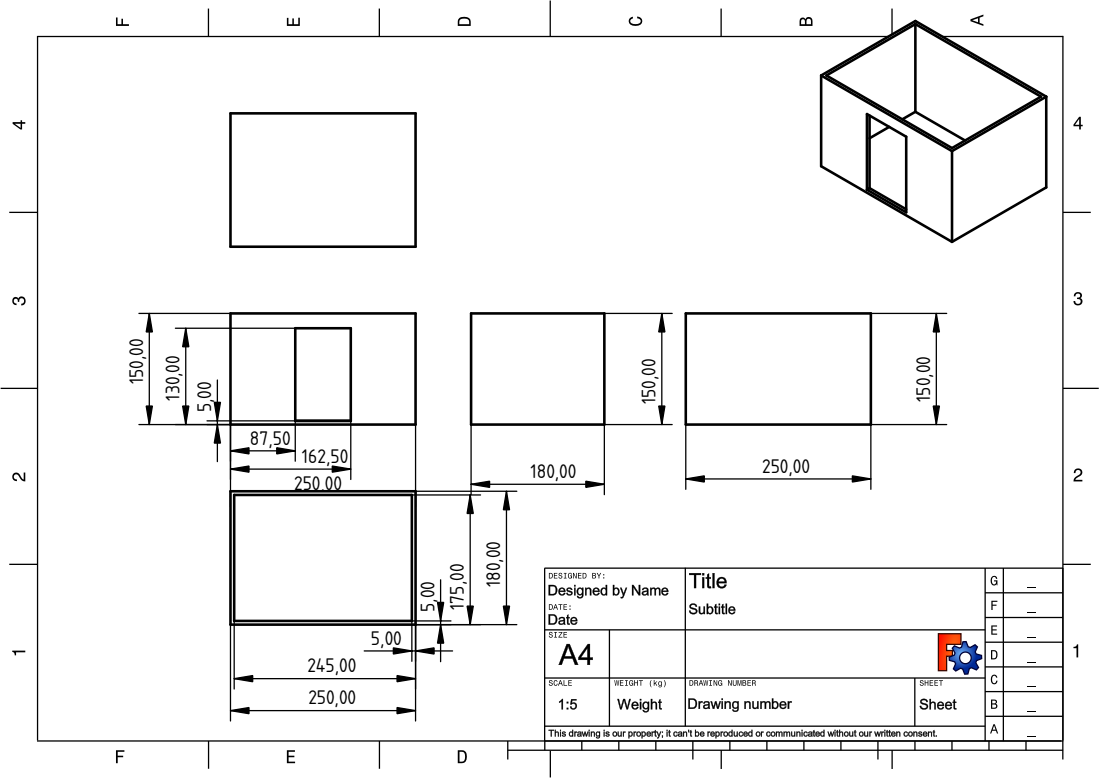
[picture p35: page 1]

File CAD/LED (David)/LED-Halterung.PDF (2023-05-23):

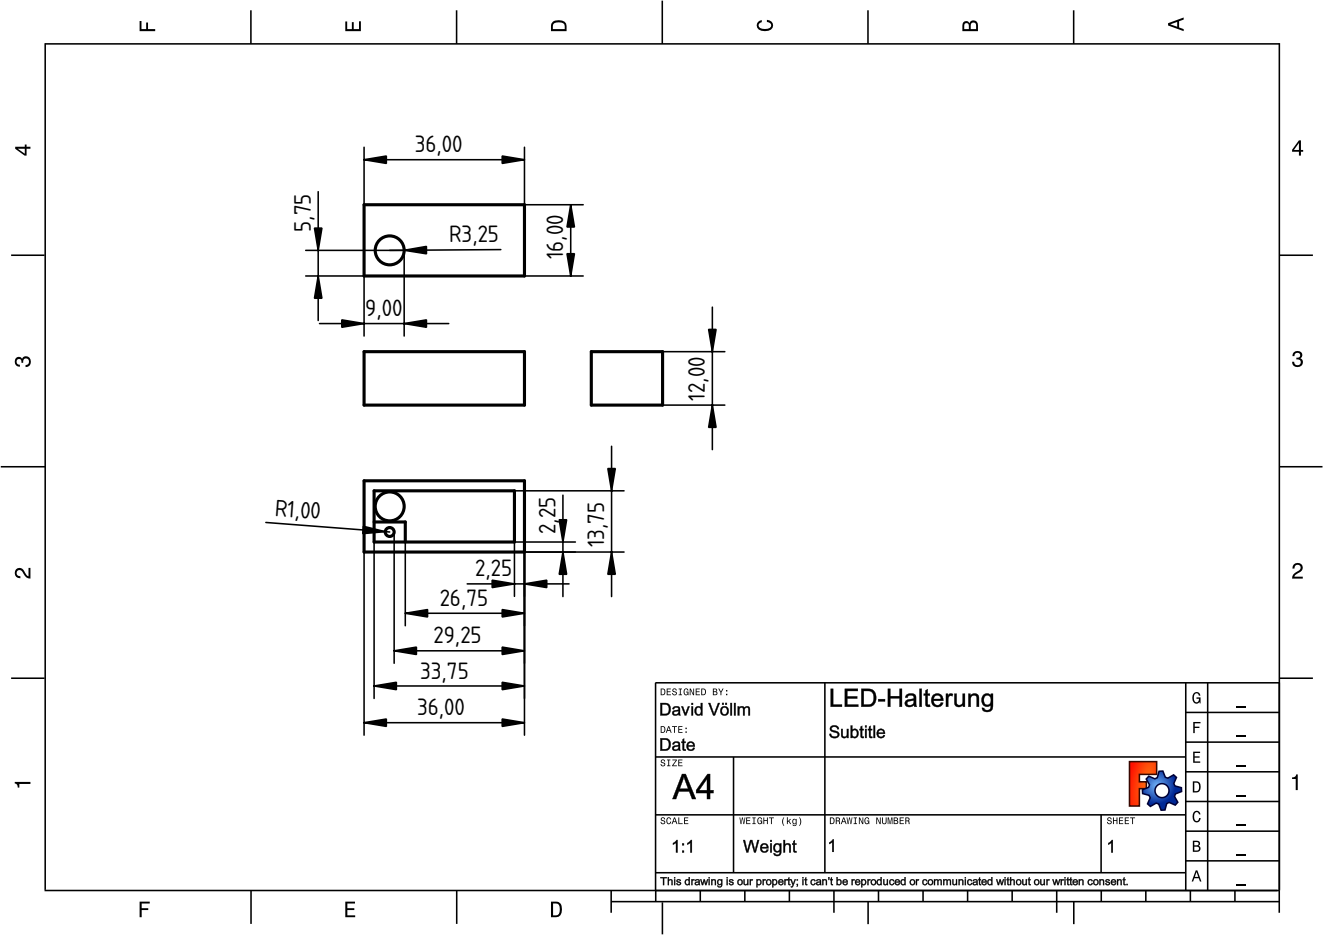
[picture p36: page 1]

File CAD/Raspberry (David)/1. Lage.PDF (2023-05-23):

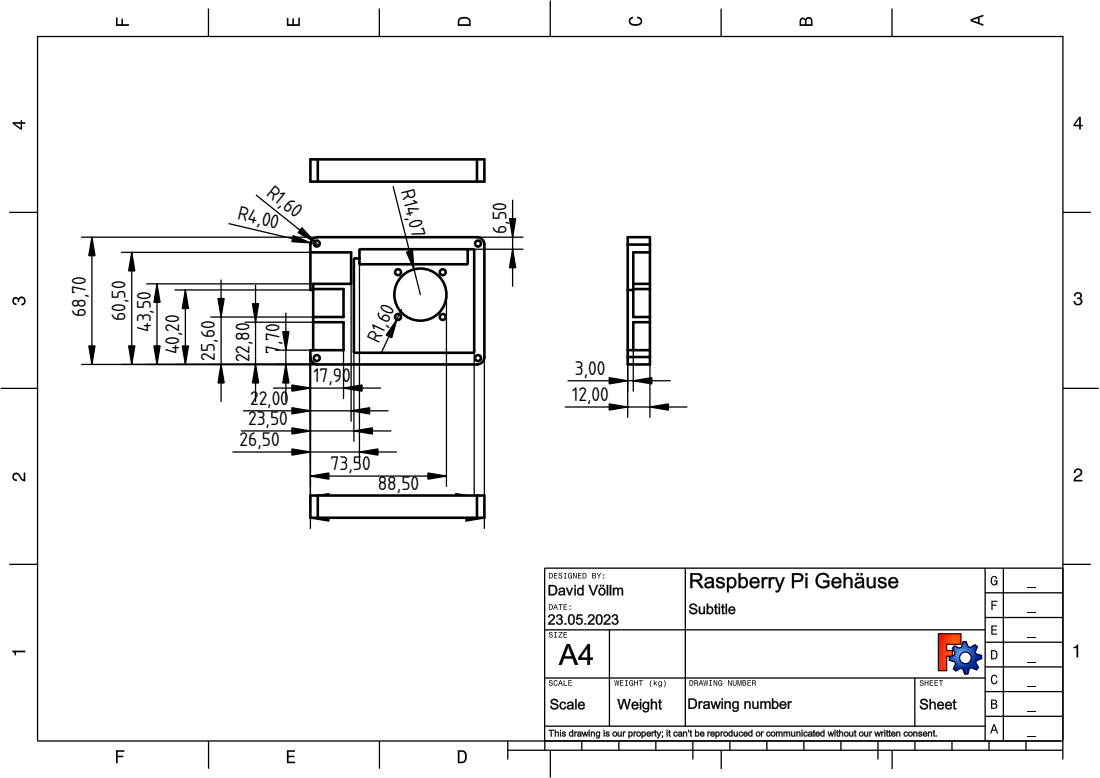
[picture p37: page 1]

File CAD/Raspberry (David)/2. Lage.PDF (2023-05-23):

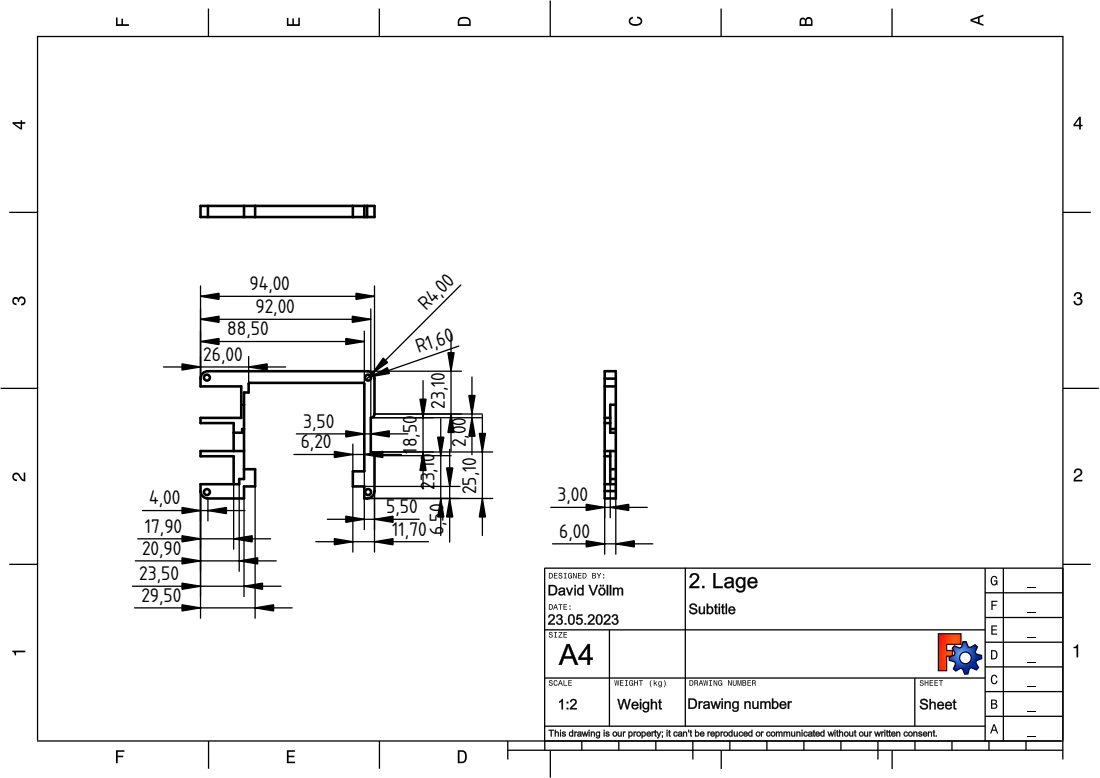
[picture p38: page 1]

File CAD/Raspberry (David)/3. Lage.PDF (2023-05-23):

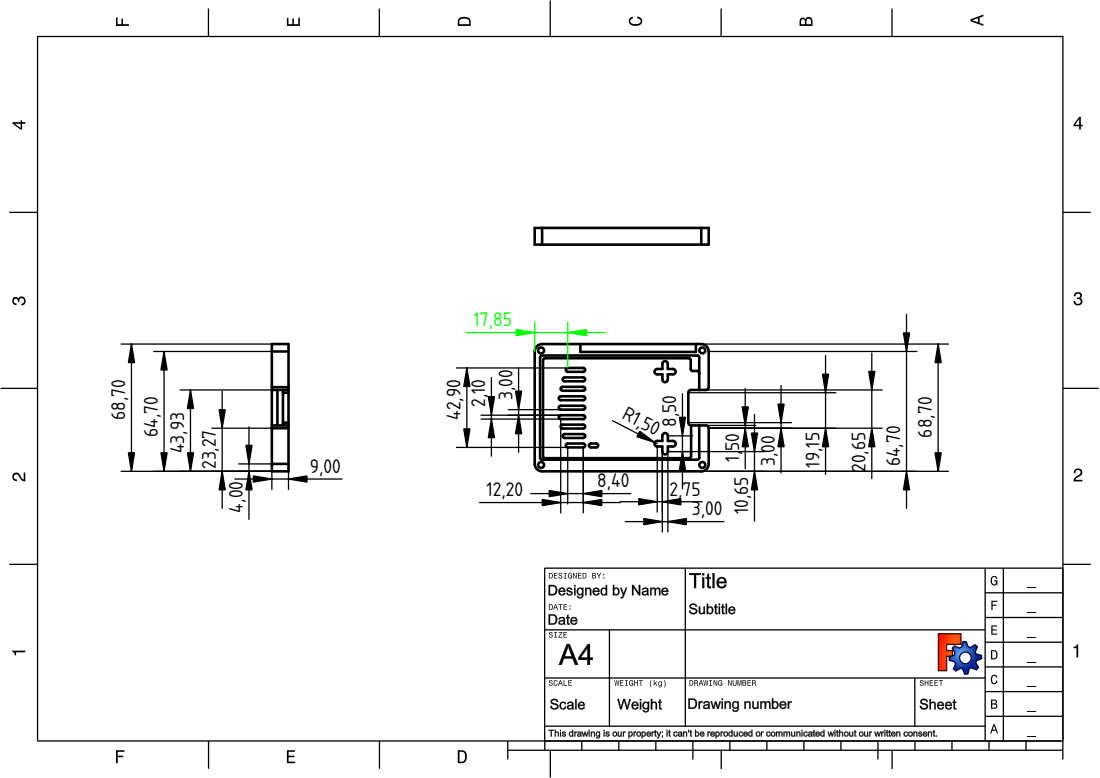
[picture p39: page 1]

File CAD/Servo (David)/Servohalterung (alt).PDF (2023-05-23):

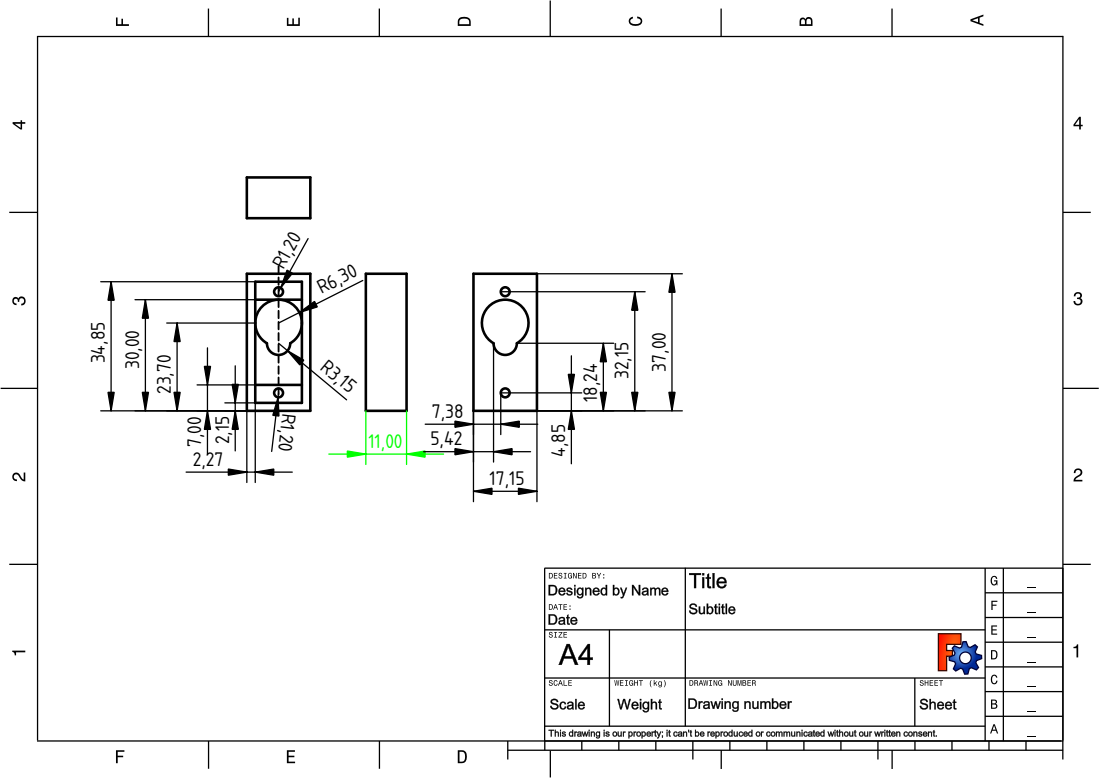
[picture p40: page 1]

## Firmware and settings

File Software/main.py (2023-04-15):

from handler import Handler
from Bibliotheken import * # Importiert alle Bibliotheken aus dem Ordner Bibliotheken

GPIO.setmode(GPIO.BCM) # Damit wird nur festgelegt wie die Ports nummeriert werden (in diesem Fall wie in pinBelegung.png in den orangenen Kästen)
GPIO.setwarnings(False) # unnötige Meldungen entfernen

# Handler Objekt wird erstellt und Pins der einzelnen Bauteile können definiert werden
handler = Handler(Buzzer(pin=17), LED(rot=2, gruen=3,blau=4), Servo(pin=27), Camera(0), PersonenHandler(),Gesichtserkennung(), Knopf(pin=26), Knopf(pin=19)) 
# Handler Initialisiert alles nötige
handler.begin()

print("ready") # Debugging Information

try: # Falls ein Fehler auftritt oder das Programm bewusst unterbrochen wird stürzt das Programm nicht ab
    while True: # Programm soll fortlaufen wiederholt werden
        handler.loop() # Hauptschleife des Handlers wird aufgerufen
except Exception as e:
    print('Error', str(e)) # Fehlerausgabe

handler.end()

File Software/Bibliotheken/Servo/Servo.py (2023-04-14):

import RPi.GPIO as GPIO
import time

class Servo:
    def __init__(self, pin, frequency = 50):
        self.pin = pin
        GPIO.setup(pin, GPIO.OUT) # Pin als Output festlegen
        self.p = GPIO.PWM(pin, frequency) # PWM Objekt erstellen um Servo zu steuern
        self.p.start(0)
    def setAngle(self, angle:float): # Servo in gewünschten Winkel ausrichten
        pos = 2+(angle/18) # Durch Recherche und ausprobieren herausgefunden: dadurch dreht sich der Servo genau auf den gewünschten Winkel
        self.p.ChangeDutyCycle(pos)
        time.sleep(0.5)
        self.p.ChangeDutyCycle(0)
    def stop(self):
        self.p.stop()

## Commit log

2023-02-20 Designed Servo for later constructions
    [Servo.FCStd]
2023-02-21 moved CAD files in folder
    [Kasten.FCStd, Servo.FCStd]
2023-02-21 added screw holes
    [Servo.FCStd]
2023-02-21 Designed Servohalterung
    [Servohalterung.FCStd]
2023-02-21 moved screw holes
    [Servohalterung.FCStd]
2023-02-21 Build Servo together
    [Servo_Zusammenbau.FCStd]
2023-02-21 updated Servohalterung to fit better
    [Kasten.FCStd, Servo_Zusammenbau.FCStd, Servohalterung.FCStd]
2023-03-01 Reorganized files
    unusefull ones got deleted
    [Servohalterung-Body.stl]
2023-03-02 Kasten Erneuert
    [Kasten (2).FCStd]
2023-03-02 Servo ansteuerung mit beispiel
2023-03-02 added fan
2023-03-13 Platinen Design anfgefangen
    [Platine.fzz]
2023-03-15 added all components
    [Platine.fzz]
2023-03-16 moved max files and created Schanier concept
    [16_02_2023_Max_Davd_J2.stl, Kasten (2).FCStd, Kasten.FCStd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]
2023-03-16 started LED-Gehäuse
    [LED Halterung.FCStd]
2023-03-16 moved CAD files in folders and completed LEDHalterung
    [LED Halterung-Body.stl, LED Halterung.FCStd, LED Zusammenbau.FCStd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]
2023-03-16 deleted unused cad-files
    [Kasten (2).FCStd]
2023-03-16 print(names) for testing
2023-03-16 removed debug print
2023-03-16 take frame raw
2023-03-16 save taken frame as jpg
2023-03-16 camera and personenHandler are in StrukturSoftware
2023-03-16 all essentials for evaluating camera output
2023-03-16 finished Buzzer lib and created example use
    [Buzzer.py]
2023-03-16 updated led
2023-03-16 other buzzer
    [Platine.fzz]
2023-03-17 ledgehäuse fertig
2023-03-20 loop und Personenberechtigungen
2023-03-30 Alle Sensoren und akteure ansteuern
2023-04-14 Lüftungsgehäuse fertig
    [1. Lage-Body.stl, 1. Lage.FCStd, 2. Lage-Body.stl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]
2023-04-14 Ablauf fertig und vollständig; kommentiert
2023-04-14 cleanup am Ende und kommentiert
2023-04-14 Updated TODO and specified camera
2023-04-14 changed pin Layout
2023-04-14 warten bis Tür geöffnet wurde
    damit sie nicht sofort wieder verschlossen wird
2023-04-14 Created image of circuit
2023-04-14 finished circuit diagram
    created a folder for all circuit stuff
    [Platine.fzz, Schaltplan.fzz]
2023-04-15 LED ausschalten am Schluss
2023-05-20 Doku verbessert und Durführung geschrieben
2023-05-20 pin Layout for older Raspberry Pi
2023-05-20 program for testing the camera
2023-05-23 added Tuerstopper and uploaded tutorial
    [Kasten.FCStd, Türstopper.FCStd]
2023-05-23 added techsketch and start up tutorial
    [1. Lage-Body.stl, 1. Lage.FCStd, 2. Lage-Body.stl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]
